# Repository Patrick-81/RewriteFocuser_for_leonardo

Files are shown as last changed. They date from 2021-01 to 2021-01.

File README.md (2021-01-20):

# RewriteFocuser_for_leonardo

## Pré-requis

* Installer VS code qui est l'outil de codage pour le firmware https://code.visualstudio.com/download
* Installer dans VS code le plugin platformio https://platformio.org/install/ide?install=vscode
* Ouvrir un compte EasyEDa pour réaliser les circuits (fihiers json) stockés dans le réperoire Schémas ou les rédessiner à partir des fichiers pdf

## Fichiers de conception du circuit imprimé.
* Ouvrir dans EasyEDA les fichiers json situés dans le répertoire Schémas.
* Les composants à acquérir sont dans le fichier : BOM_test2-2_2021-01-17.csv

## Compilation du firmware
* Ouvrez VSCode dans lequel vous avez installé l'extension platformIO
* clonez le répertoire Github and un répertoire de votre choix : git clone https://github.com/Patrick-81/RewriteFocuser_for_leonardo
* Entrez dans le repertoire RewriteFocuser_for_leonardo ou master_RewriteFocuser_for_leonardo
* Windows: double cliquez sur le fihier platformio.ini ==> le projet devrait se charger dans l'extension platformio de VSCode
* Linux : à partir de VSCode chargez le répertoire (Open Folder). Répondre par la négative à la question posée par la fenêtre popup.
* Linux & windows : 
	* compilez le code en cliquant sur la coche en bas à gauche de la page
	* Branchez votre arduino au port USB du PC, vérifiez le port USB sur lequel vous êtes connectés, si nécessaire modifiez la définition du port dans upload_port dans le fichier platformio.ini
	* téléversez le firmware vers l'arduino en utilsant la flèche "->" en bas à gauche de l'écran.
## c'est fini...

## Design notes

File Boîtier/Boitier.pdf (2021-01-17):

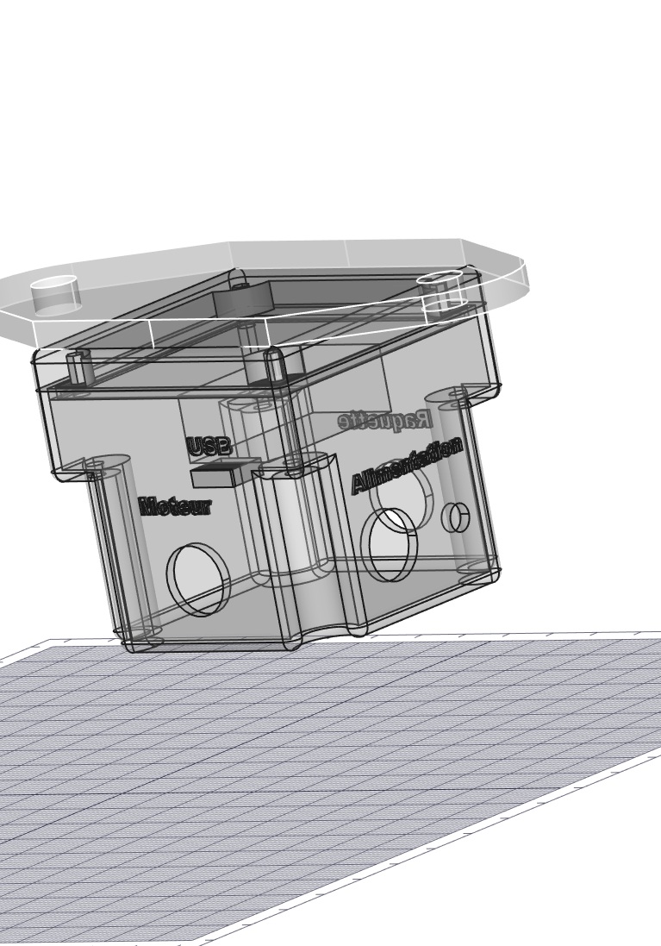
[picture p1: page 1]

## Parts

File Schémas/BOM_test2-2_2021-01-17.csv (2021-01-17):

ID | Name | Designator | Footprint | Quantity | Manufacturer Part | Manufacturer | Supplier | Supplier Part | Digi-Key
1 | 100uF | C1 | CAP-D8.0XF3.5 | 1 | ECA-1HM101 | Panasonic | Mouser | 667-ECA-1HM101B | P5182-ND
2 | DRV8825 Stepper Motor Driver Carrier | U2 | DRV8825 STEPPER MOTOR DRIVER CARRIER | 1
3 | Arduino_Pro_Micro | U1 | ARDUINO_PRO_MICRO | 1 | Arduino Pro Micro
4 | XH-3A | BOUTONS-MAP1 | XH-3A | 1 | XH-3A | BOOMELE | LCSC | C2316
5 | LM7805 | IC1 | TO220 | 1
6 | 1k | R1 | AXIAL-0.3 | 1
7 | XH-2A | INPUT-12V,LED1 | XH-2A | 2 | XH-2A | BOOMELE | LCSC | C20079
8 | MOTOR | CN1 | XH-4A | 1 | XH-4A | BOOMELE | LCSC | C37815
9 | I2C | CN2,CN3 | XH-4A | 2 | XH-4A | BOOMELE | LCSC | C37815

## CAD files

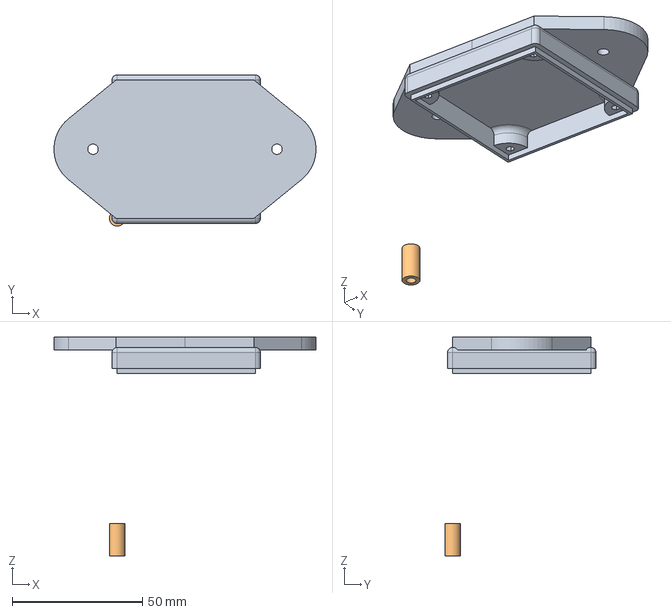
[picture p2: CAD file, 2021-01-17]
Boîtier/Boitier.FCStd
100.5 x 58.0 x 84.0 mm
couvercle
Cale

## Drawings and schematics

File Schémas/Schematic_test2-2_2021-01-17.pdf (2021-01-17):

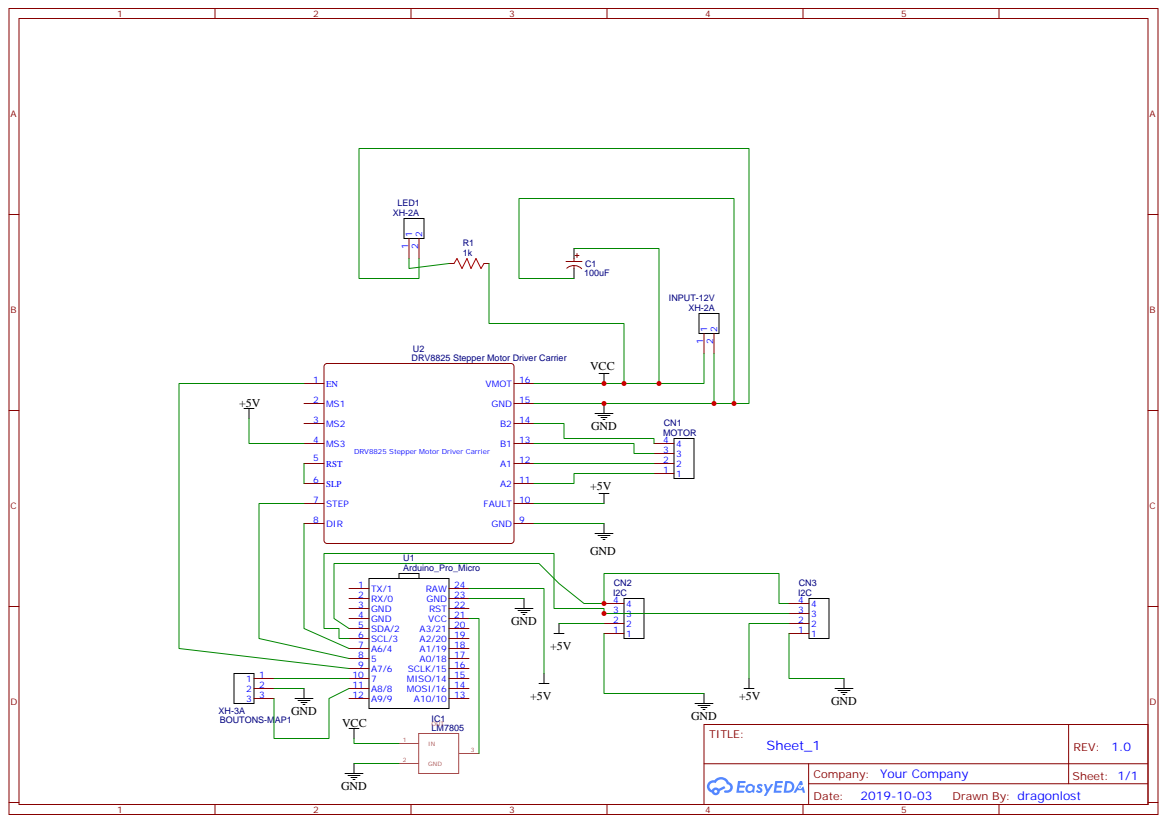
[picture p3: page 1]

DRV8825 Stepper Motor Driver Carrier

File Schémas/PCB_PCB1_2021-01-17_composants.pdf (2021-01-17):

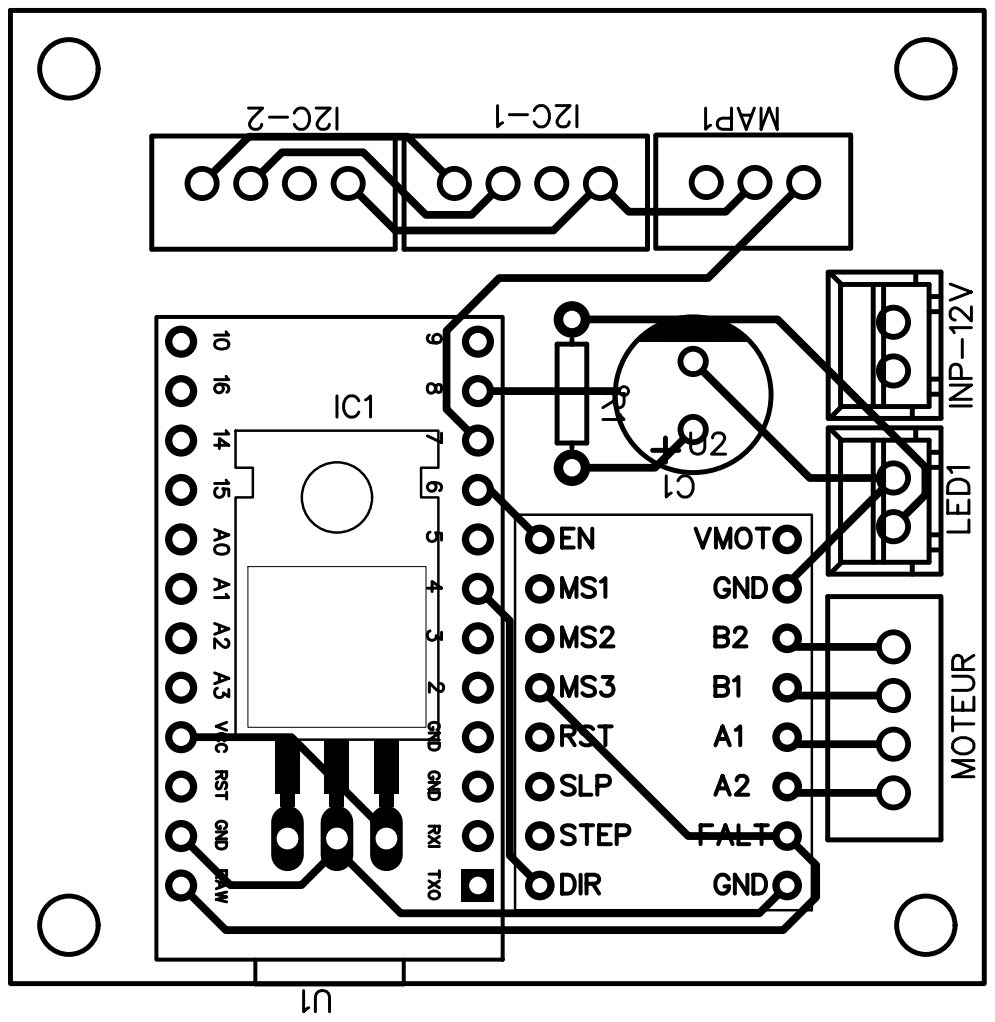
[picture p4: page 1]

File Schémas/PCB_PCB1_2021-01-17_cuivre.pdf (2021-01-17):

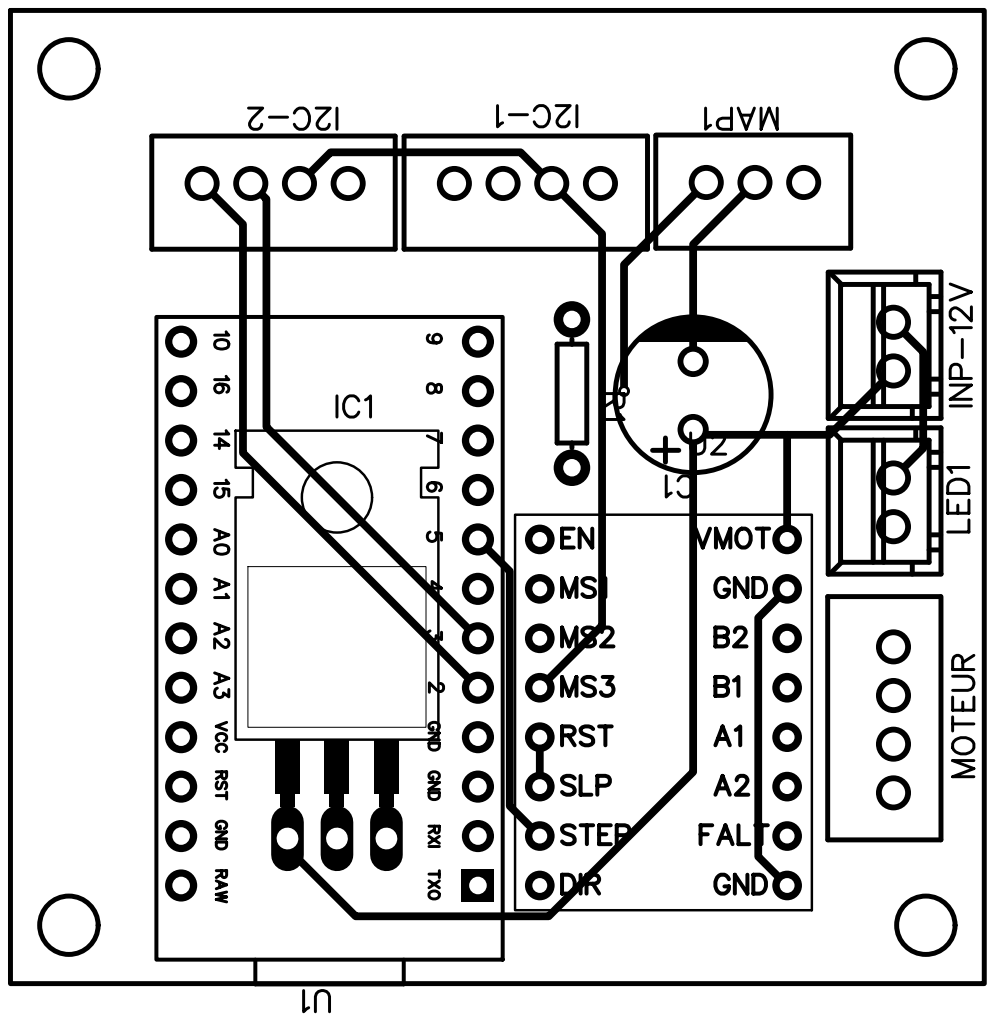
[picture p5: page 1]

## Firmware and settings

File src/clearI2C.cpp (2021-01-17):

/**
 * I2C_ClearBus
 * (http://www.forward.com.au/pfod/ArduinoProgramming/I2C_ClearBus/index.html)
 * (c)2014 Forward Computing and Control Pty. Ltd.
 * NSW Australia, www.forward.com.au
 * This code may be freely used for both private and commerical use
 */

//#include <Wire.h>

/**
 * This routine turns off the I2C bus and clears it
 * on return SCA and SCL pins are tri-state inputs.
 * You need to call Wire.begin() after this to re-enable I2C
 * This routine does NOT use the Wire library at all.
 *
 * returns 0 if bus cleared
 *         1 if SCL held low.
 *         2 if SDA held low by slave clock stretch for > 2sec
 *         3 if SDA held low after 20 clocks.
 */
#include <Arduino.h>

int I2C_ClearBus() {
#if defined(TWCR) && defined(TWEN)
  TWCR &= ~(_BV(TWEN)); //Disable the Atmel 2-Wire interface so we can control the SDA and SCL pins directly
#endif
  pinMode(SDA, INPUT_PULLUP); // Make SDA (data) and SCL (clock) pins Inputs with pullup.
  pinMode(SCL, INPUT_PULLUP);

  delay(2500);  // Wait 2.5 secs. This is strictly only necessary on the first power
  // up of the DS3231 module to allow it to initialize properly,
  // but is also assists in reliable programming of FioV3 boards as it gives the
  // IDE a chance to start uploaded the program
  // before existing sketch confuses the IDE by sending Serial data.

  boolean SCL_LOW = (digitalRead(SCL) == LOW); // Check is SCL is Low.
  if (SCL_LOW) { //If it is held low Arduno cannot become the I2C master. 
    return 1; //I2C bus error. Could not clear SCL clock line held low
  }

  boolean SDA_LOW = (digitalRead(SDA) == LOW);  // vi. Check SDA input.
  int clockCount = 20; // > 2x9 clock

  while (SDA_LOW && (clockCount > 0)) { //  vii. If SDA is Low,
    clockCount--;
  // Note: I2C bus is open collector so do NOT drive SCL or SDA high.
    pinMode(SCL, INPUT); // release SCL pullup so that when made output it will be LOW
    pinMode(SCL, OUTPUT); // then clock SCL Low
    delayMicroseconds(10); //  for >5uS
    pinMode(SCL, INPUT); // release SCL LOW
    pinMode(SCL, INPUT_PULLUP); // turn on pullup resistors again
    // do not force high as slave may be holding it low for clock stretching.
    delayMicroseconds(10); //  for >5uS
    // The >5uS is so that even the slowest I2C devices are handled.
    SCL_LOW = (digitalRead(SCL) == LOW); // Check if SCL is Low.
    int counter = 20;
    while (SCL_LOW && (counter > 0)) {  //  loop waiting for SCL to become High only wait 2sec.
      counter--;
      delay(100);
      SCL_LOW = (digitalRead(SCL) == LOW);
    }
    if (SCL_LOW) { // still low after 2 sec error
      return 2; // I2C bus error. Could not clear. SCL clock line held low by slave clock stretch for >2sec
    }
    SDA_LOW = (digitalRead(SDA) == LOW); //   and check SDA input again and loop
  }
  if (SDA_LOW) { // still low
    return 3; // I2C bus error. Could not clear. SDA data line held low
  }

  // else pull SDA line low for Start or Repeated Start
  pinMode(SDA, INPUT); // remove pullup.
  pinMode(SDA, OUTPUT);  // and then make it LOW i.e. send an I2C Start or Repeated start control.
  // When there is only one I2C master a Start or Repeat Start has the same function as a Stop and clears the bus.
  /// A Repeat Start is a Start occurring after a Start with no intervening Stop.
  delayMicroseconds(10); // wait >5uS
  pinMode(SDA, INPUT); // remove output low
  pinMode(SDA, INPUT_PULLUP); // and make SDA high i.e. send I2C STOP control.
  delayMicroseconds(10); // x. wait >5uS
  pinMode(SDA, INPUT); // and reset pins as tri-state inputs which is the default state on reset
  pinMode(SCL, INPUT);
  return 0; // all ok
}
/*

void setup() {
  // put your setup code here, to run once:
  Serial.begin(9600);

  int rtn = I2C_ClearBus(); // clear the I2C bus first before calling Wire.begin()
  if (rtn != 0) {
    Serial.println(F("I2C bus error. Could not clear"));
    if (rtn == 1) {
      Serial.println(F("SCL clock line held low"));
    } else if (rtn == 2) {
      Serial.println(F("SCL clock line held low by slave clock stretch"));
    } else if (rtn == 3) {
      Serial.println(F("SDA data line held low"));
    }
  } else { // bus clear
    // re-enable Wire
    // now can start Wire Arduino master
    Wire.begin();
  }
  Serial.println("setup finished");
}

void loop() {
  // put your main code here, to run repeatedly:
  // do Wire RTC stuff here.
}
*/

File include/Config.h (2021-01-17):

#ifndef Config_h
#define Config_h

// ----- General config -----
// Status LED pin
#define LED 13
#define SERIAL_SPEED 9600
#define ENABLE_SW_RS false

// ----- Stepper driver configuration -----
// Motor driver type: BasicStepperDriver (0), DRV8825 (1), A4988 (2) or DRV8834 (3)
#define STEPPER_TYPE 1
// Steps per revolution
#define STEPS_REV 200
// gears reduction
#define GEARS_RED 3
// Stepper resolution
#define SINGLE_STEP 1
// Ignored for BasicStepperDriver. Can be 1, 2, 4, 8, 16 or 32
#define FULL_STEP 16
// Ignored for BasicStepperDriver. Can be 1, 2, 4, 8, 16 or 32
#define HALF_STEP 32
// Reverses the direction of the motor
#define REVERSE_DIR true
// RPM. Decreasing this value should decrease telescope shaking.
#define MOTOR_RPM 50
#define MIN_RPM 10
#define MAX_RPM 100
// Acceleration
#define MOTOR_ACCEL 1000
// Motor pulses per second (pps). See full formula here: https://electronics.stackexchange.com/a/232679
// #define MOTOR_PPS (MOTOR_RPM * STEPS_REV / 60)
// ----- Driver pins -----
#if defined(ARDUINO_AVR_NANO)
    // Driver DIR pin
    #define DRIVER_DIR 2
    // Driver STEP pin
    #define DRIVER_STEP 3

#elif defined (ARDUINO_AVR_LEONARDO)
    // Driver DIR pin
    #define DRIVER_DIR 4
    // Driver STEP pin
    #define DRIVER_STEP 5
#endif
// Driver ENABLE pin. Comment to disable functionality
#define DRIVER_EN 6
// M0. Only for microstepping-enabled drivers
#define M0 4
// M1. Only for microstepping-enabled drivers
#define M1 5
// M2. Only for microstepping-enabled drivers
#define M2 6
// Mouvement manuel in
#define INWARD 7
// Mouvement manuel out
#define OUTWARD 8
// I2C Port
#define I2CPORT 0x02

// ----- Polar finder light -----
#define ENABLE_POLAR_LIGHT false
#define POT_ANALOG_PIN 0
#define POLAR_LIGHT_LED 10

// ----- Customizable pins -----
// List of pins that can be modified by the serial port
//#define CUSTOMIZABLE_PINS {7, 8, 9}
// Backlash use
// right shift value
// The backlash value is defined by
// Backlash = StepMode * STEPS_REV * GEARS_RED
// Backlash = (Backlash >> BacklashLevel);
//
#define BACKLASHHIGH 2
#define BACKLASHMED  4
#define BACKLASHLOW  6
#
#define __DEBUG__    true

#endif

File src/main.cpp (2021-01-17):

#include <Arduino.h>
#include "parser.h"

extern bool USB_present;

long time1;
long time2;
void storePos();


void setup()
{
  // put your setup code here, to run once:

  initialize(0);
  time1 = millis();
//  inithandpad();

}
void loop() {
    // Si une donnée est dispo sur le port série
    while (Serial.available () > 0)
    {
      char c = '\0';
      c = Serial.read ();
      processIncomingByte (c);
    }
  move();
}

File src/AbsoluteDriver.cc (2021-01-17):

/*
 * AbsoluteDriver - Stepper Motor Driver Driver
 * Indexer mode only.

 * Copyright (C)2015 Laurentiu Badea
 *
 * This file may be redistributed under the terms of the MIT license.
 * A copy of this license has been included with this distribution in the file LICENSE.
 */
#include "AbsoluteDriver.h"

bool forward = true;
long dep = 0;
/*
 * Microstepping resolution truth table (Page 13 of AbsoluteDriver pdf)
 * 0bMODE2,MODE1,MODE0 for 1,2,4,8,16,32 microsteps
 */
const uint8_t AbsoluteDriver::MS_TABLE[] = {0b000, 0b001, 0b010, 0b011, 0b100, 0b111};

AbsoluteDriver::AbsoluteDriver(short steps, short dir_pin, short step_pin)
:DRV8825(steps, dir_pin, step_pin)
{}

AbsoluteDriver::AbsoluteDriver(short steps, short dir_pin, short step_pin, short enable_pin)
:DRV8825(steps, dir_pin, step_pin, enable_pin)
{}

/*
 * A4988-AbsoluteDriver Compatibility map: MS1-MODE0, MS2-MODE1, MS3-MODE2
 */
AbsoluteDriver::AbsoluteDriver(short steps, short dir_pin, short step_pin, short mode0_pin, short mode1_pin, short mode2_pin)
:DRV8825(steps, dir_pin, step_pin, mode0_pin, mode1_pin, mode2_pin)
{}

AbsoluteDriver::AbsoluteDriver(short steps, short dir_pin, short step_pin, short enable_pin, short mode0_pin, short mode1_pin, short mode2_pin)
:DRV8825(steps, dir_pin, step_pin, enable_pin, mode0_pin, mode1_pin, mode2_pin)
{}

const uint8_t* AbsoluteDriver::getMicrostepTable()
{
    return (uint8_t*)AbsoluteDriver::MS_TABLE;
}

size_t AbsoluteDriver::getMicrostepTableSize()
{
    return sizeof(AbsoluteDriver::MS_TABLE);
}

short AbsoluteDriver::getMaxMicrostep(){
    return AbsoluteDriver::MAX_MICROSTEP;
}

void AbsoluteDriver::setCurrentPosition(long Target)
{
  currentPos = Target;
}
void AbsoluteDriver::moveTo(long Target)
{
  targetPos = Target;
  forward = (targetPos > currentPos ? true : false);
  dep = (targetPos-currentPos);
  startMove(dep);
}
long AbsoluteDriver::currentPosition()
{
  return (forward ? (targetPos - getStepsRemaining()) : (targetPos + getStepsRemaining()));
}
long AbsoluteDriver::targetPosition()
{
  return targetPos;
}
long AbsoluteDriver::distanceToGo()
{
  return getStepsRemaining();
}
long AbsoluteDriver::run()
{
  long remaining = nextAction();
  currentPos = (forward ? (targetPos - getStepsRemaining()) : (targetPos + getStepsRemaining()));
  return currentPos;
}
void AbsoluteDriver::startMove(long steps, long time=0)
{
  BasicStepperDriver::startMove(steps, time);
}
/*
void AbsoluteDriver::stop()
{
  BasicStepperDriver::stop();
  targetPos = currentPos;
}
*/
void AbsoluteDriver::move(long steps, uint16_t wait)
{
  BasicStepperDriver::move(steps);
  delayMicroseconds(wait);
}

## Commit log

2021-01-17 Suppression des fichiers inutiles
2021-01-17 Purge des fichiers inutiles
2021-01-17 Ajout des éléments complémentaires
    [BOM_test2-2_2021-01-17.csv, Boitier.FCStd]
